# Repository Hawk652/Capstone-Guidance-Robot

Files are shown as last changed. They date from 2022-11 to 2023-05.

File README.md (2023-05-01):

# Greeting and Guidance Robot

## Executive Summary

Entering a building for the first time can be confusing. An insuffieicnt amount of information is typically provided to help one traverse a new building. With the new Ashraf Islam Engineering Buidling that is currently being built for Tennessee Technological University, the same issues will occur. The focus of the capstone project is to provide a solution to the problem. The solution is a autonoumous greeting and guidance robot that will assist people in navigating the Ashraf Islam Engineering Building. 

## Capabilities

Our final product is capable of mapping and navigating an area whilst avoiding collisions. It can reroute its path and always ensure that the user gets to the room that they are wanting to go to as well as return to its starting location once it's finished.

## Salient Outcomes

We learned that bluetooth 5.2 location services is not very accesible at the consumer level as of yet outside of heavy research or recent products. It's the reason why we ended up having to change to ultra wideband triangulation for location verification. We're also going to be learning about and implementing near field sensors as close range location verification with the assistance of Dr. Charles Van Neste More stuff will get added as we actually assemble the project.

## Project Demonstration

[Video demonstration of our Capstone project!](https://youtu.be/Icbw_ISEM2E)

## About Us

### Team
[Samuel Mandody](
https://www.youtube.com/watch?v=M5V_IXMewl4) - Knowledgeable in Embedded Systems. Strong fundamental coding skills and quick learner. Will be working on the locomotion subsystem and everywhere else coding related.

[Gabriel Kim](https://www.youtube.com/watch?v=dQw4w9WgXcQ) - Electrical engineering major with a focus on smaller electronics. Working mainly on the main control subsystem.

Emma Brown - Enjoys designing and implementing hardware. Willing to research and a fast learner. In charge of the safety subsystem.

[Andre Nguyen](https://www.youtube.com/watch?v=l60MnDJklnM) - Electrical Engineering major with a focus on power. In charge of the power subsystem. The designated team leader.

[Jacob Wilkinson](https://www.youtube.com/watch?v=GQHVQvePdtI) - Electrical and Computer Engineering major with a focus on embedded software development. In charge of user interface.

### Faculty Supervisor

Dr. Charles Van Neste

### Stakeholders

Dr. Andy Pardue is the customer and individual who came up with the idea for this project. Occupants of the Ashraf Islam Building alike will benefit from the guidance robot. 

### Recognitions 

A special thank you to:
Tristain Hill for providing us with the Turtlebot

Dr. Stephen Canefield for assisting us with the software implementation of the robot.

## Repo Organization

### [Reports](https://github.com/Hawk652/Capstone-Guidance-Robot/tree/main/Reports)
The section contains the project proposal documents and the conceptual design and planning documents.

### [Documentation](https://github.com/Hawk652/Capstone-Guidance-Robot/tree/main/Documentation)
The section contains the 3D models, electrical files, images related to the project, and signoffs.
#### [3D Models](https://github.com/Hawk652/Capstone-Guidance-Robot/tree/main/Documentation/3D%20Models)
#### [Electrical](https://github.com/Hawk652/Capstone-Guidance-Robot/tree/main/Documentation/Electrical)
#### [Images](https://github.com/Hawk652/Capstone-Guidance-Robot/tree/main/Documentation/Images)
#### [Signoffs](https://github.com/Hawk652/Capstone-Guidance-Robot/tree/main/Documentation/Signoffs)

### [Software](https://github.com/Hawk652/Capstone-Guidance-Robot/tree/main/Software)
The section will contain all software related to the project.

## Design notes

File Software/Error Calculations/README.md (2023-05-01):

# Error Calculations for Trilateration
## Function
This script runs a random amount of points in a range and calculates the error of the robot at that location. This assumes a specific placement of beacons and requires that the max error for each beacon is 10cm. The error is calculated for many points and the max error for all tested points is shown. This should prove the accuracy of the system.
## Dependencies
The only dependencies for this software is the default Matlab libraries
## How to Install
Matlab can be downloaded from the Mathworks website: https://matlab.mathworks.com/
Once downloaded, run the executable.
## How to Run
Run using the run button in Matlab's editor tab.

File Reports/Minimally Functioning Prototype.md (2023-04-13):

# Minimally Functioning Prototype

## Locomotion
Enclosures for the new stepper motors were designed and printed. Unfortunately, the new stepper motors will not be utilized because the motor controllers will not be arriving in on time.

## Safety
The robot is able to prevent collision with an object or wall.

## Localization
ESP32 beacons were able to communicate with each other and relay positional data. The ESP32 beacons were used instead because the ultra-wideband beacons will not be arriving in on time. 

## Power and Charging
The chaging subsystem is able to transform AC power from a receptacle into DC power and deliver it to the robot's power subsystem. The buck converters in subsystem is able to deliver 12 V at the output. However, the power subsystem will not have the desired battery due to ordering issues. 

## User Interface
The robot is able to move around and change directions with the use of voice commands through a microphone.

## Main Control
The robot is able to take commands from the user interface subsystem and use the LIDAR and motors to move around in its environment.

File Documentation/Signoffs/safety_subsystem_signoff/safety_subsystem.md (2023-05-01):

# Safety Subsystem

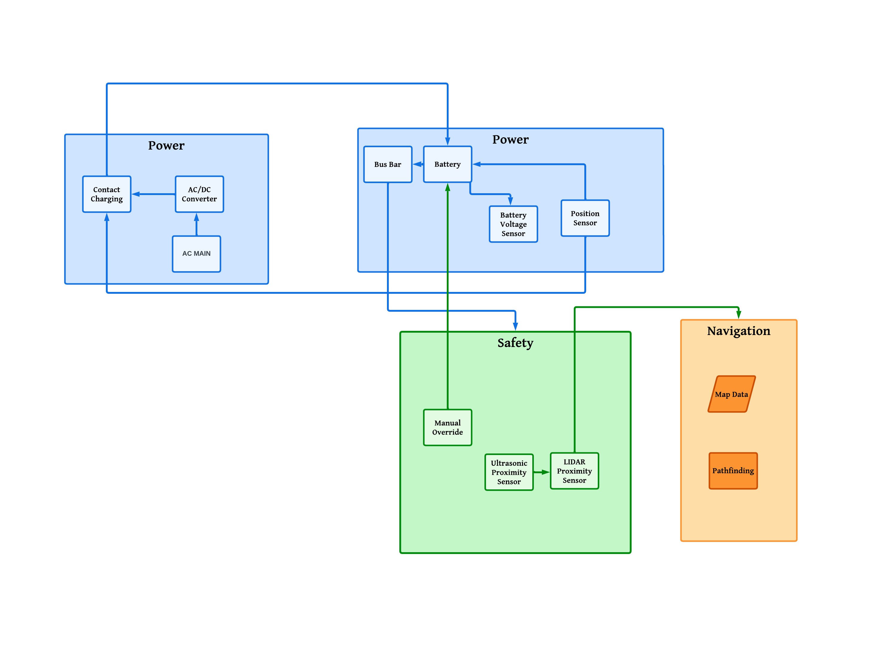
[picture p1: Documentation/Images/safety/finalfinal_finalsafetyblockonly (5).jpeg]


#  Function of the Subsystem

 The safety Subsystem will be tasked with obstacle avoidance, a manual override, and utilizing the LIDAR’s mapping capabilities. The sensors and button will be attached to the top of  the robot, that way it can utilize “seeing” capabilities. The sensors will gather information within the range (0.5 meters) of  robot and send this information to the Arduino or Raspberry PI.  To ensure that there will be no obstacle undetected, the LIDAR and Proximity sensor, ultrasonic  will be utilized to ensure redundancy. When an obstacle is detected within the range by the proximity sensor, ultrasonic sensor and the LIDAR, the information will be transmitted to the Main Control subsystem.  The LIDAR will be using its mapping capabilities to determine if the robot is too close to walls, doors, and corners. The proximity sensor will be using a 360 obstacle avoidance technique to determine the location of the obstacle. The DDS module will take the signal from a crystal oscillator and use it as a clock to create a buffer output waveform at a specific frequency that is set by the onboard microcontroller.  The Grove - Ultrasonic Distance Sensor will be using a range of  3cm - 350cm by using a non-contact form of measurement. 

#  Constraints
| No. |Constraint  |  Origin  |
|-|-|-|
|1|  Shall have manual override (power will be cut from the motor) |Supervisor: Dr. Van Neste |
|2 |Shall maintain a distance of 0.5 m from obstacles and people |Broader Implication |

#  Buildable Schematics
##  Subsytsem Schematic

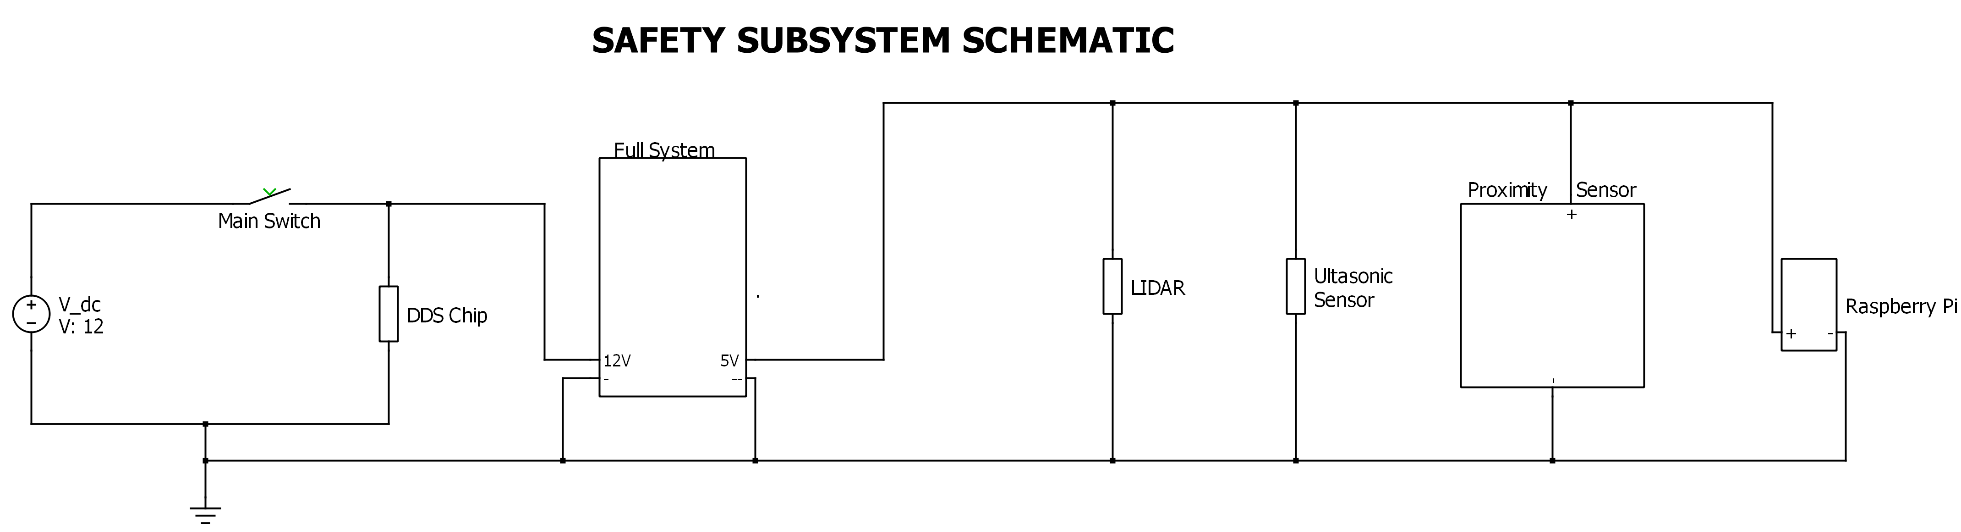
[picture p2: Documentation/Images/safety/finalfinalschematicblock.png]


This schematic illustrates all the components that will be interacting with one another in this system. Each of these sections will be covered throughout this document. 

## Pinout of the Subsystem
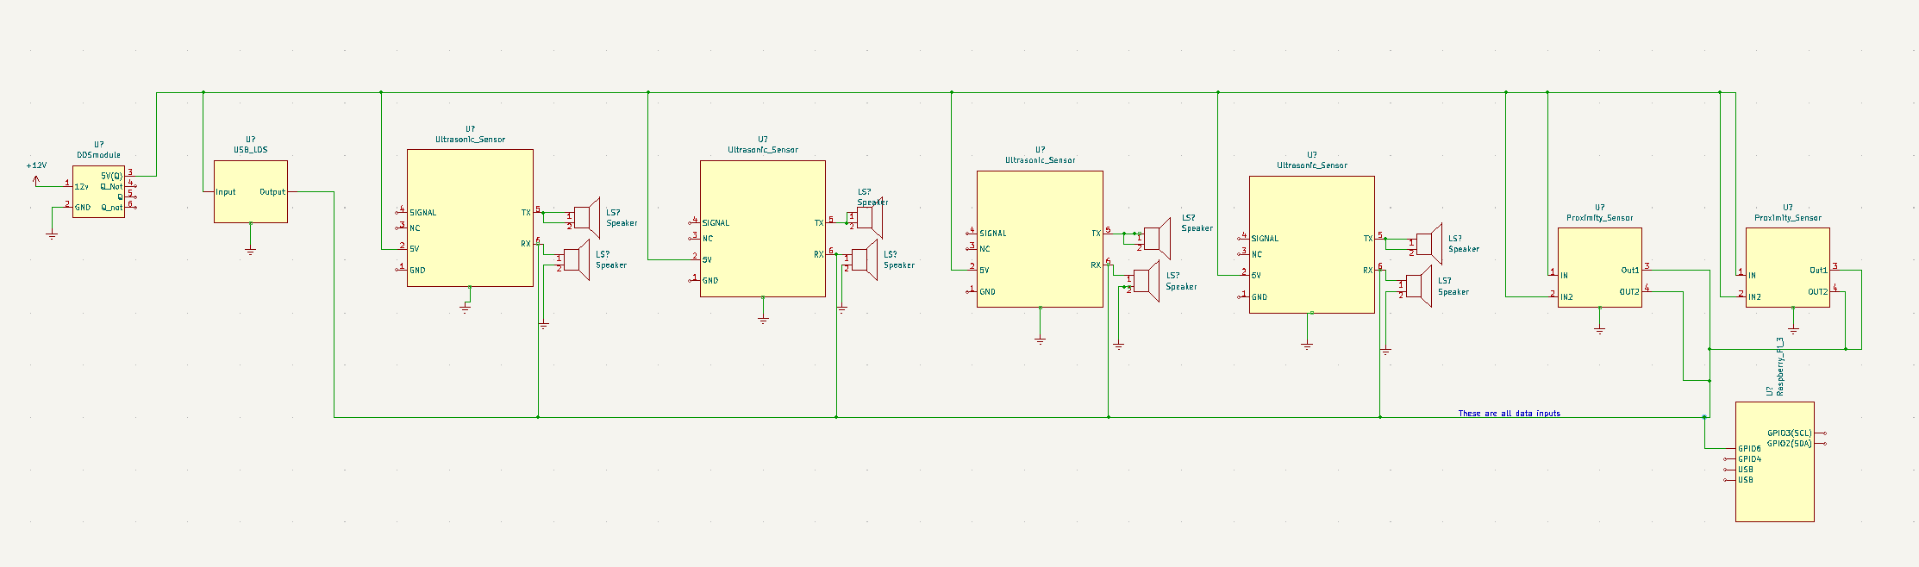
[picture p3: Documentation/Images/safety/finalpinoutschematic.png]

##  Near Field Sensor (Proximity Sensor)
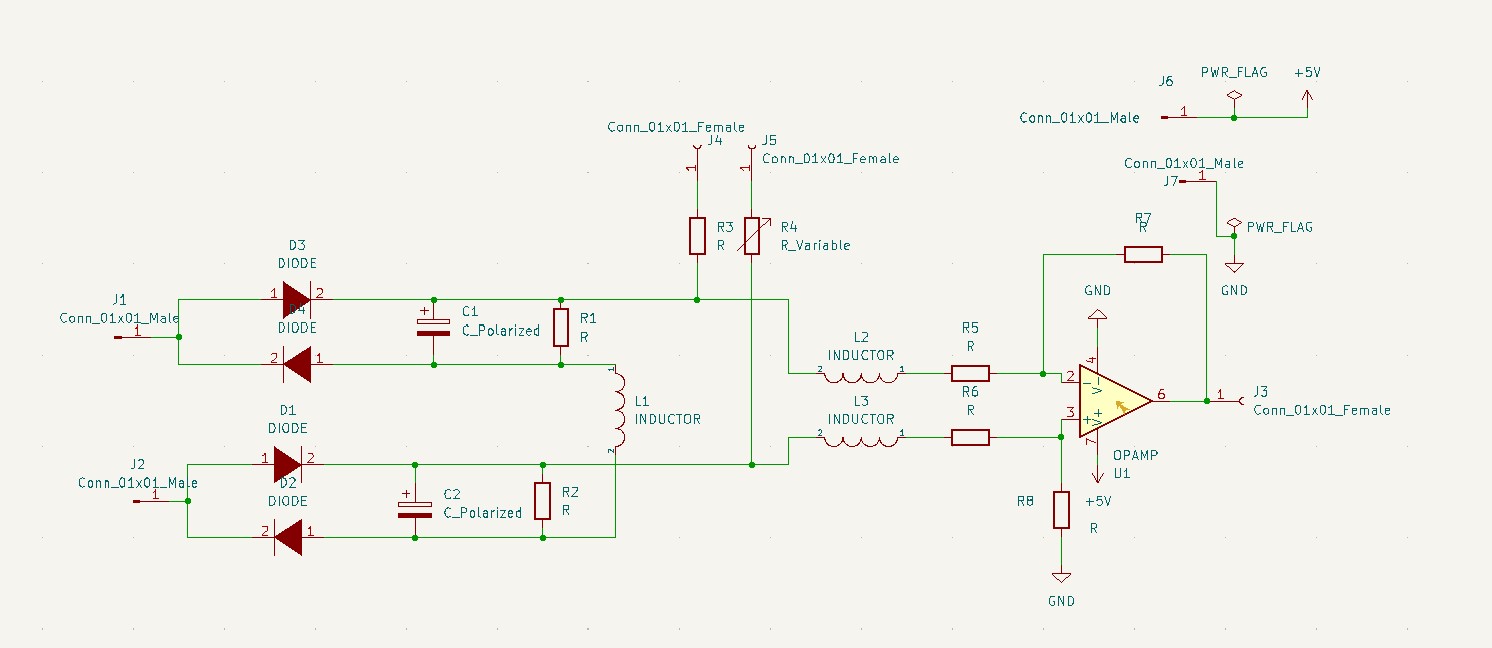
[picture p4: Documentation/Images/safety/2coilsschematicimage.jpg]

The Proximity Sensor will be the main safety sensor for this subsystem. This sensor will be able to detect objects in an omnidirectional field of view. This sensor will be accomplished by the implementation of coils. By using their electric fields, the sensors will be able to detect very small changes in their distance. Below are the specific values that will be used for each component and are necessary for the sensor to function properly. These specific values have been researched in “Capacitive omnidirectional position sensor using a quarter wave resonator,” and discussed with Dr. Van Neste to ensure that these should be correct. 

### Table of Components 
|Component| Value| Unit|
|-|-|-|
|D1-D4 |1N4001|-|
|C1,C2  |4.7|μF|
|R1,R2| 1|kΩ|
|L1,L2,L3 |300|μH|
|R4,R5 |2|kΩ|
|R6,R7 |20|kΩ|

## Image of PCB 
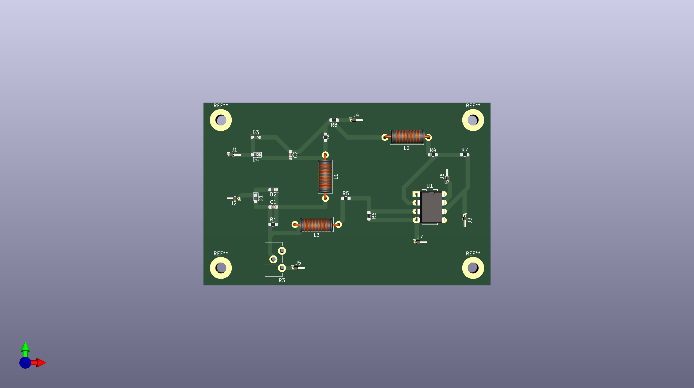
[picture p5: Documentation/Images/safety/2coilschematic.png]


front side
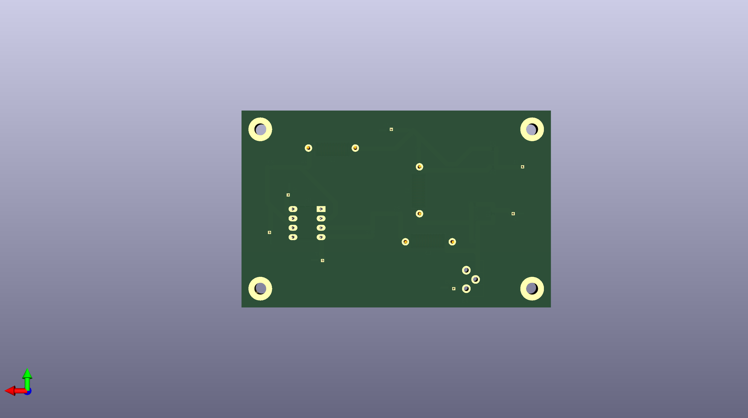
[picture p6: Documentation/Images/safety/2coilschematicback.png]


back side

### 3d Model of Attachement to Robot
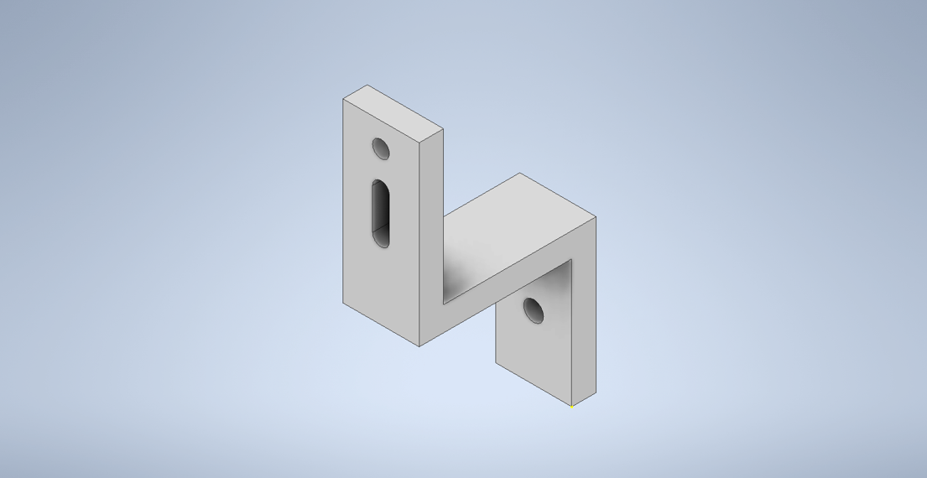
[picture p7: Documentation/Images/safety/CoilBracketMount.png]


### Reasoning for Proximity Sensor
After extensive research and discussions with Dr. Van Neste, this sensor seemed to be the best for the Autonomous Guidance Robot. Currently, there are not any sensors on the market that would be within the price range of this project. The best option was to build an omnidirectional sensor with the help of Dr. Van Neste. This sensor will enable the robot to detect any obstacles or people that might stand in the way of the robot and be able to avoid the detections that have been obtained. 

#  Ultrasonic Sensor
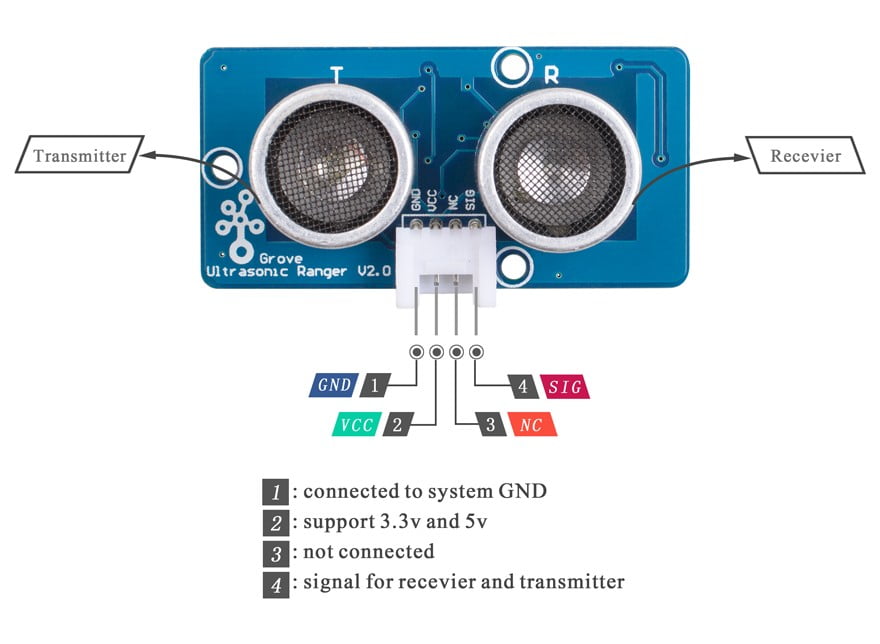
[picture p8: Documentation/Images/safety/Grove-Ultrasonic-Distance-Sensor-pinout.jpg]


The Grove - Ultrasonic Distance Sensor will be implented as the ultrasonic sensor for this subsystem.This item will be a backup sensor for the Proximity sensor. 

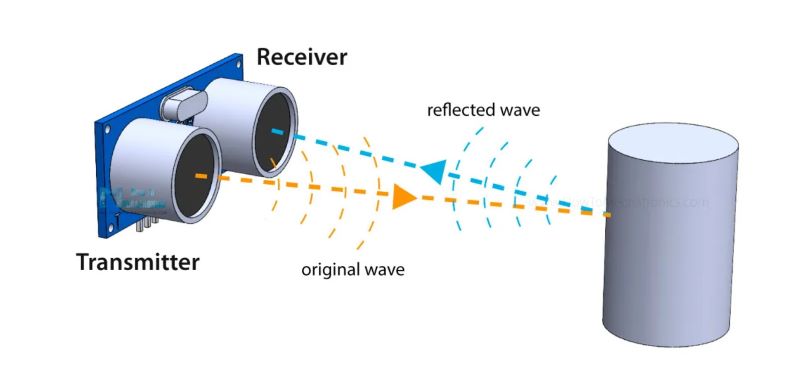
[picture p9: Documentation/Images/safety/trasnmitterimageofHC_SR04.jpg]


The reasoning for this is because the Proximity sensor will have a better range and has a radial sensing method than the ultrasonic sensor. The ultrasonic sensor determines an object's distance by sending a form of sonar waves out and determines the distance from the receiving signal that reflects off of an object that is within the range of the sensor, which is 3cm to 350cm. 

## Pinout of Ultrasonic Sensor
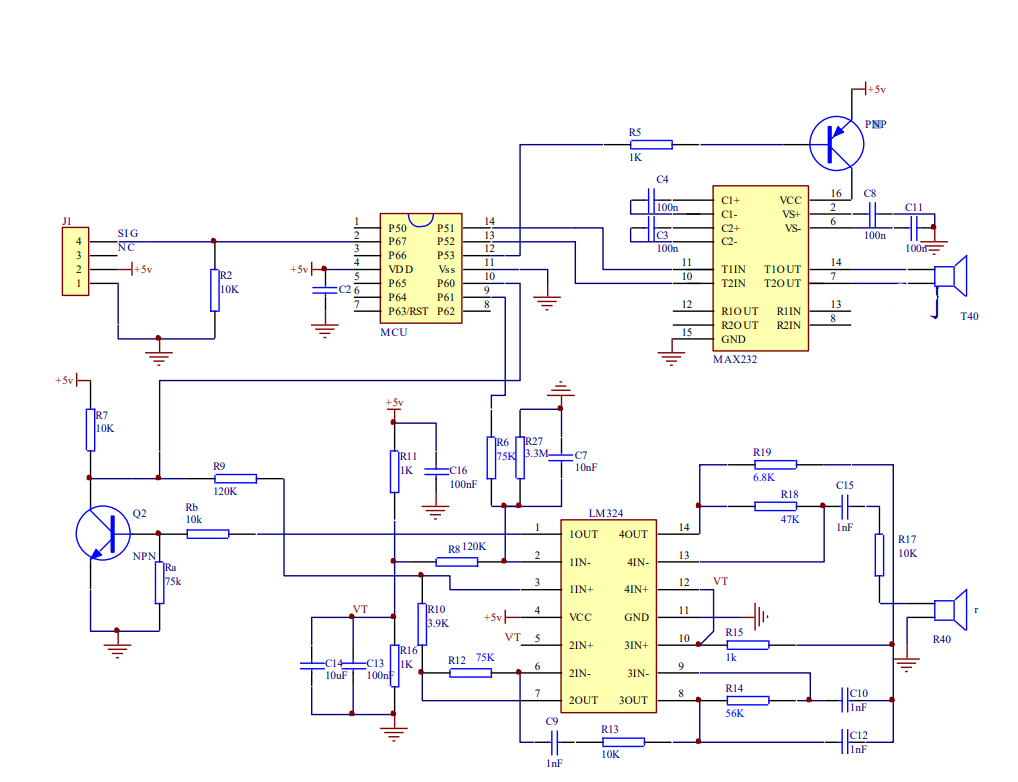
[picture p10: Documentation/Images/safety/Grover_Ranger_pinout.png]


|Component| Value| Unit|
|-|-|-|
|Operating Voltage|DC 3.2~5.2V|-|
|Operating Current |8|mA|
|Operating Frequency| 40|KHz|
|Min Range |3 |cm|
|Max Range |350|cm|
|Accuracy|2|mm|
|Measuring Angle |<15|°|
|Dimmension|50 x25 x16|mm|
 
# DDS Module 
The DDS module is going to create a sinusoidal wave to get the coil to resonate. This module will generate a sine waveform then this signal will be sent to the coil.

# LIDAR
The LIDAR component will be implemented for the robot's safety and surroundings. The LIDAR will determine where the walls, corners, and doors are. The robot will be aware of the floor layout and will be able to differentiate obstacles compared to structures. The details on how this device works and how it will be implemented in the rest of the system will be in the Localization Subsystem.

# Raspberry Pi
The brain of the robot will be the Rasperry Pi. This means that all of the components in this subsystem will send all of their information back to the Raspberry Pi. The details on how this device works and how it will be implemented in the rest of the system will be in the Main Control Subsystem.

# Main Switch

The main switch's functionality will be to quickly cut off power to the robot for emergency purposes. This switch wil be located on the outside of the robot that way the robot can be shut off manually. The switch will be discussed further in the Power Subsystem.

#   Analysis

The safety Subsystem (SubsystemBlockDiagram) is a schematic of how the subsystem will connect with one another and to the Main control subsystem. The main switch will be connecting directly to the Battery (12V), this will turn off everything in an event of an emergency. The DDS module runs off of the same voltage and will go through a DC/DC converter to reduce the voltage to be 5V.  Once the voltage as been converted to 5V the power of  the rest the Safety subsystem. The LIDAR,
Grove - Ultrasonic Distance Sensor, Proximity Sensor, and the Raspberry Pi will be all be connected  in parallel with one another. The LIDAR is further discussed in detail within the Localization subsystem. The Grove - Ultrasonic Distance Sensor is used to ensure that the robot will detect an object within a range of 3cm - 350cm. The output of the subsystem will be sent to the Raspberry Pi. The proximity sensor will be using three electric magnetic resonators to detect changes in the electric field. By using the electric field sensor it can detect objects in close proximity, therefore creating a collision avoidance sensor.  

#    BOM
|Item| Quantity| Price Per Item| Total Price
|-|-|-|-|
|DDS Module |4|$50|$200 | |
|Grove - Ultrasonic Distance Sensor  |4|$3.95| $15.80 |
|LDS-01(LIDAR)| 1 |$200|Already Purchased
|Copper Wire |1|$54.82| $ 54.82  |
|Raspberry Pi |1|$35 |Already Purchased  |
|Total Price|||$270.62|
#    Reference

“Capacitive omnidirectional position sensor using a quarter wave resonator,” IEEE Xplore. [Online]. Available: https://ieeexplore.ieee.org/document/9827944. [Accessed: 21-Nov-2022]. 

“Data Sheet - SparkFun Electronics.” [Online]. Available: https://cdn.sparkfun.com/datasheets/Sensors/Proximity/apds9960.pdf. [Accessed: 22-Nov-2022]. 

“Grove - ultrasonic distance sensor,” Seeed Studio, 29-Dec-2022. [Online]. Available: https://www.seeedstudio.com/Grove-Ultrasonic-Distance-Sensor.html. [Accessed: 03-Feb-2023].

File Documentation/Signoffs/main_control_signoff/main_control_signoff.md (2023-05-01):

# Main Control Subsystem

## Functionality of the Subsystem
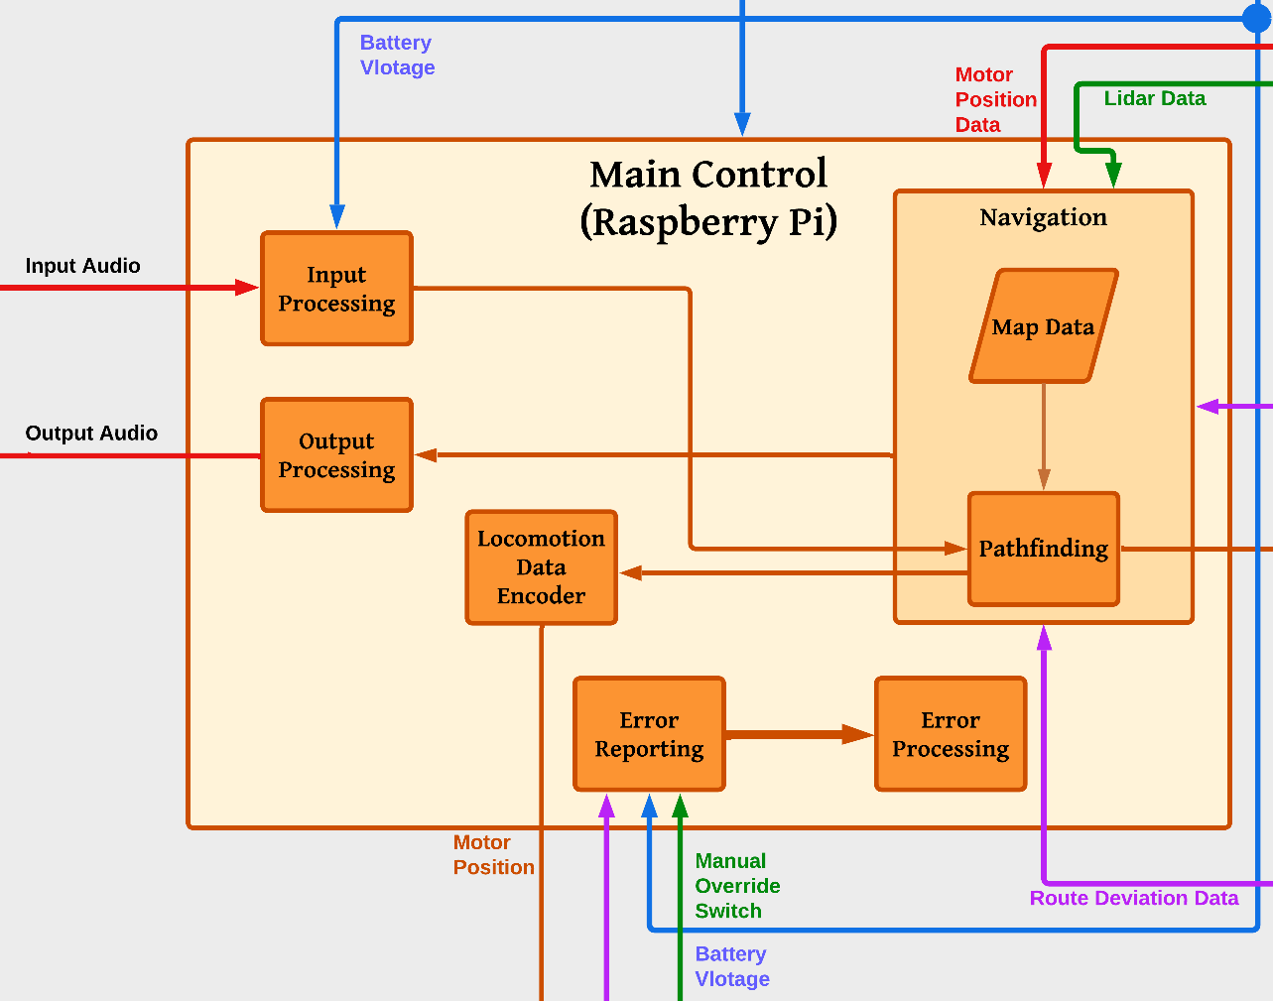
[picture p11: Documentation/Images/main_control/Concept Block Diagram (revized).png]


The main control subsystem's function is to receive inputs from the AuR's other subsystems and use those inputs to determine the AuR's actions. The subsystem is responsible for navigation and pathfinding as well as connecting all of the subsystems together.

## Specifications and Constraints
| No. | Specifications and Constraints | Origin |
|-|-|-|
| 3 | Shall operate on one floor only | Supervisor: Dr. Van Neste |
| 6 | Shall not operate below 15-20% of the battery capacity | Ethics |

## Buildable Schematic
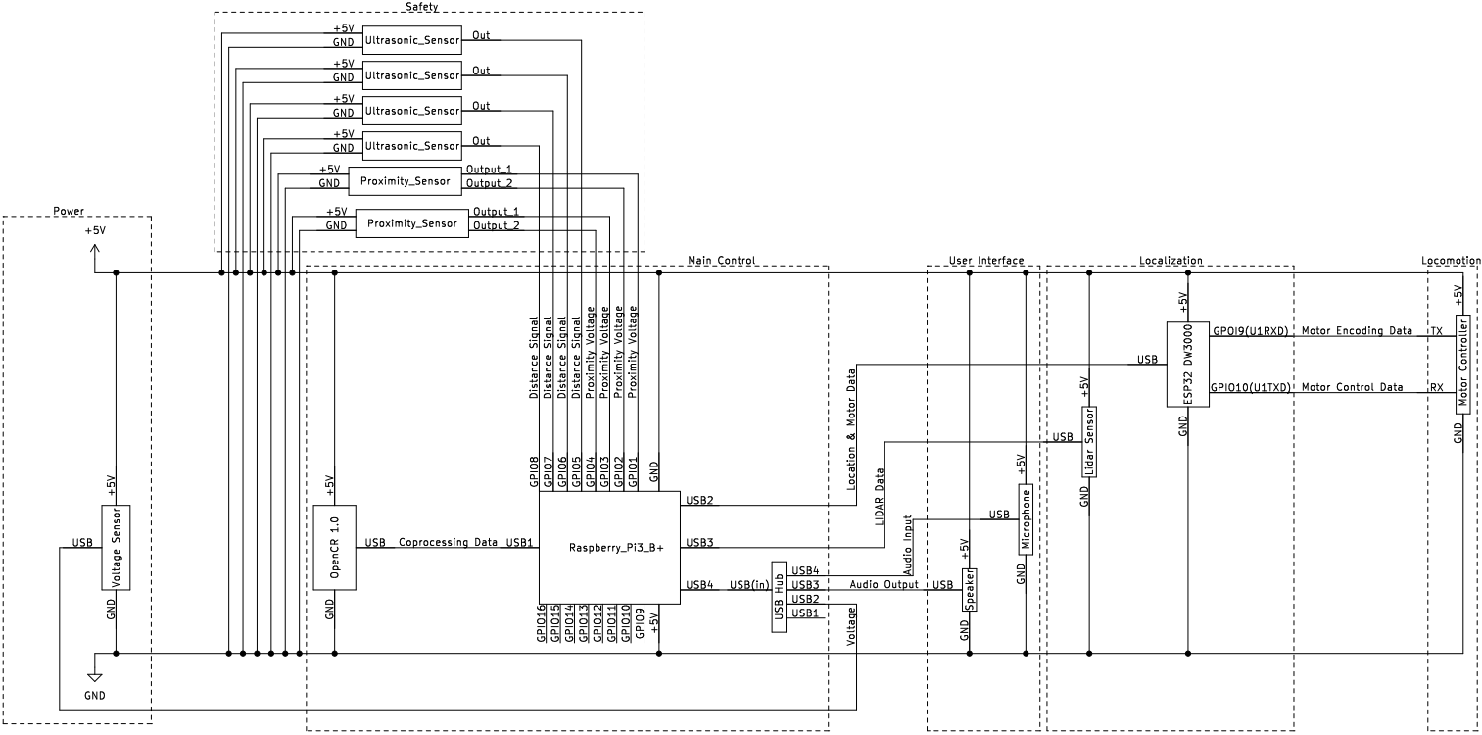
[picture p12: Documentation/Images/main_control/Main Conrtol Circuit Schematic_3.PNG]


## Analysis

### Flow Chart
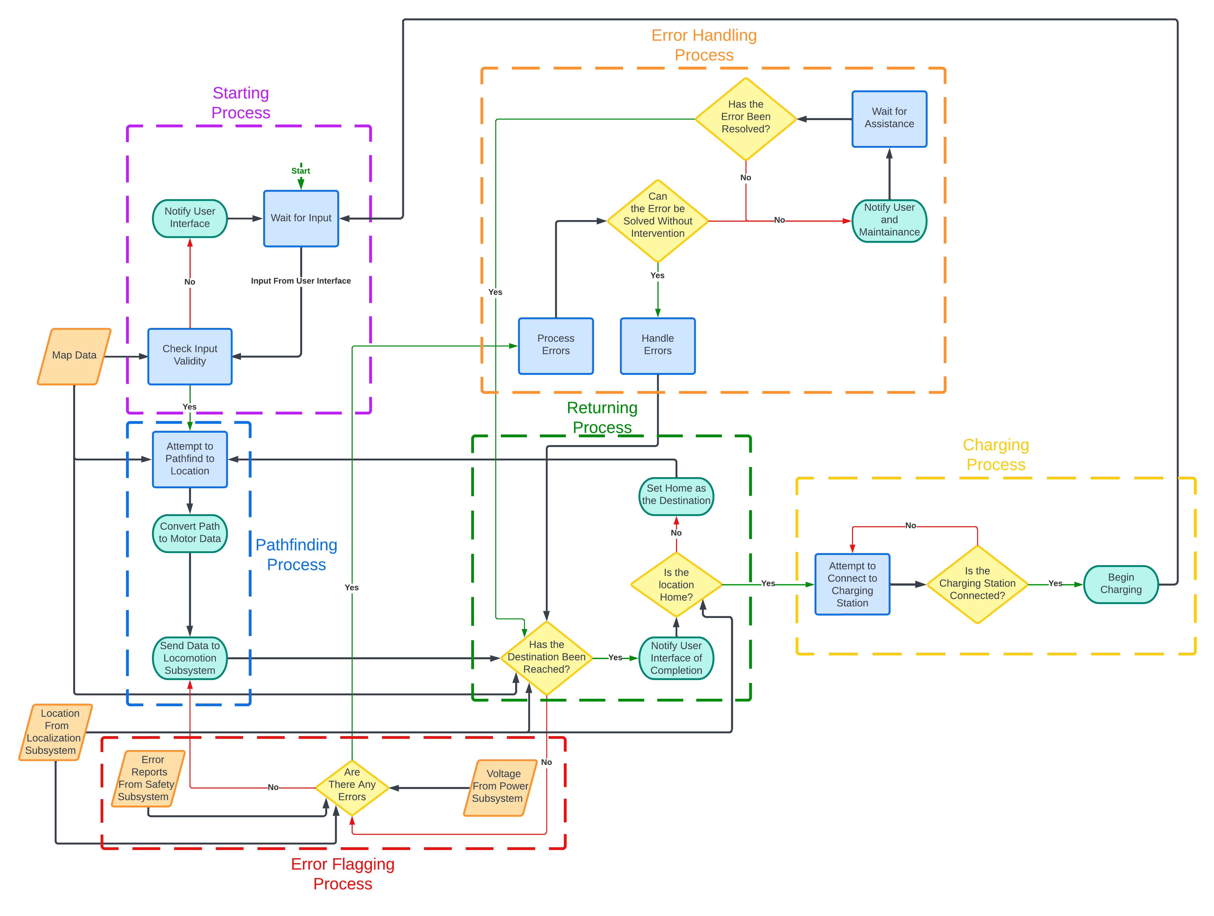
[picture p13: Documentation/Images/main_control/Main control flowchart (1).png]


### Navigation
The main control will receive location data and route deviation data from the localization subsystem as well as locomotion data from the rotary encoder. This data will be used to build and update a map model of the building. The user input will be processed in conjunction with the localization data to construct a path from the AuR's location to its desired destination. This will take place using tools provided by the ROS2 OS.
### User Input/Output
The main control will receive an input from the user interface subsystem and process that input into a usable format. The processed data will be a destination which the main control will use for its pathfinding process. An output is generated based on the status of the AuR and sent to the user interface subsystem.
### Error Processing
The main control will receive inputs from the safety, localization, and power subsystems. It will compare these inputs to expected values and if there is a discrepancy, an error will be reported. The error or errors will then be processed and a course of action will be determined based on number of errors, error details, severity of errors, and other data provided to or processed by the main control subsystem.
### Power
The Raspberry Pi3 B+ is connected to 6 devices via the four usb ports with a usb expansion port as well as 8 devices via the GPIO pins. Current output for each of the four onboard usb ports is limited to 500mA meaning the maximum output for four ports together would be 2A, however total current draw from all usb ports is limited to 1.5A[1]. GPIO pins can safely draw 50mA meaning the maximum output for 8 pins togeter would be 400mA or 0.4A. A total current draw of 2A and a voltage of 5V results in a 10 Watt load, which is doubled in order to ensure adequate battery life. This means the power subsystem must provide 20 Watts to the Main Control subsystem.
### OS
The Raspberry Pi3 B+ will be running a version of ROS2 Foxy which is based on Ubuntu 20.04. While the specific hardware requirements are not listed, the version used is a custom image provided by Robotis explicitly for use with the Raspberry Pi 3 B+[2].

## BOM
| Item | Quantity | Price Per Item | Total Price |
|-|-|-|-|
| Raspberry Pi 3 B+ | 1 | $35 | Purchased |
| USB Hub | 1 | $7.99 | $7.99 |
| | | Total Subsystem Cost: | $7.99 |

# References
[1]“Raspberry Pi Documentation - Raspberry Pi hardware,” www.raspberrypi.com. https://www.raspberrypi.com/documentation/computers/raspberry-pi.html#maximum-power-output (accessed Jan. 29, 2023).

[2]Y. Name, “ROBOTIS e-Manual,” ROBOTIS e-Manual. https://emanual.robotis.com/docs/en/platform/turtlebot3/sbc_setup/#sbc-setup

[3]“Raspberry Pi 3 Model B+.” [Online]. Available: https://static.raspberrypi.org/files/product-briefs/Raspberry-Pi-Model-Bplus-Product-Brief.pdf (Accessed: Nov. 20, 2022)

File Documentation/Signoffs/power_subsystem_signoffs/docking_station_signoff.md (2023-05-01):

# Docking Station Subsystem

## Function of the Subsystem
The function of the docking station subsystem is provide a area for the AuR to autonomously recharge power when needed.

## Specifications and Constraints

| No. | Specifications and Constraints | Origin | 
|-|-|-|
| 1 | Shall have plugless charging | Supervisor: Dr. Van Neste 
| 2 | Shall follow proper wire gauging standards | NEC 310.16(b)

## Buildable Schematic 
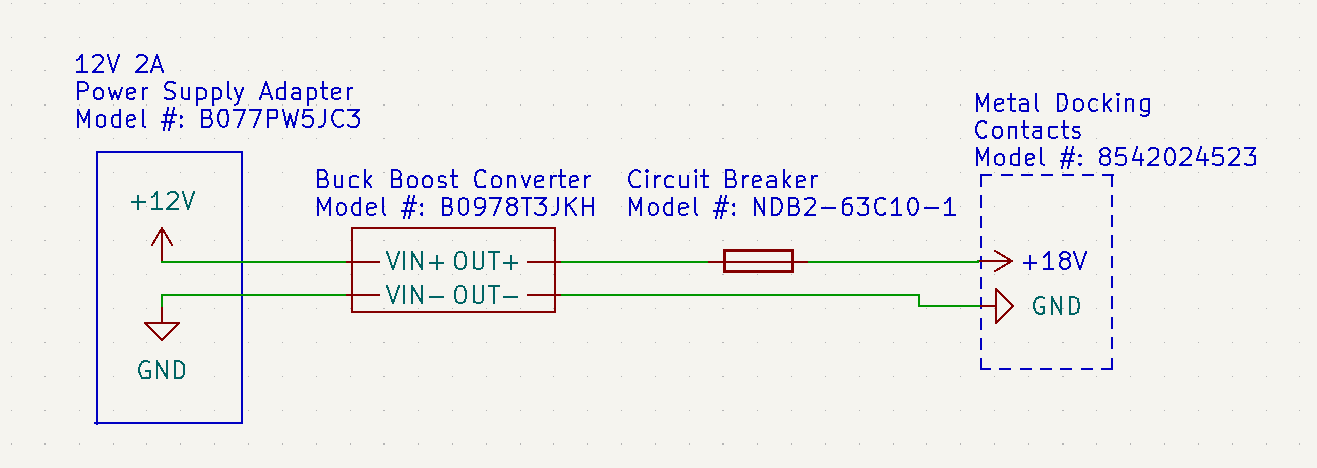
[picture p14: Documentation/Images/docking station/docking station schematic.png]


The docking station subsystem will recieve power from a 120 VAC receptacle. The 120 VAC will be converted into 12 VDC through the use of a power supply AC adapter. The 12 VDC will then be sent to buck booster to be step up to 18 VDC to match the battery voltage. Then the 18 VDC is sent to the metal contacts for the AuR to recieve power. A circuit breaker is added in to provide overcurrent protection to the circuit in the case of a short circuit happening. The buck booster converter has a functioning switch implemented which allows a user to cutoff power to the metal contacts. 

The power supply adapter will feed into the circuit through a hole on the side of the docking station's box wall. The circuit breaker  will be mounted using velcro so it does not move around. There is enough room in the box to house the breaker. A hole is created in the lid of the docking station to provide a place for the buck boost converter to mount. This will allow a user to adjust the buck boost converter and switch the circuit on and off with ease. There are two 19 mm x 15 mm holes for the metal docking contacts to be placed in.  

#### 3D Model of Charging Station
The docking station follows the same idea as receptacles by having two indentations to house the active metal contacts within the docking station. By having the metal contacts embedded into the docking station, it would be more difficult for users and other objects to accidentally touch both active metal contacts. The indentations additionally assist in guiding the AuR into the correct position when recharging. A wire can fed through a hole on the side of the charging station and reach the metal contacts from within the docking station.

##### Front Isometric View
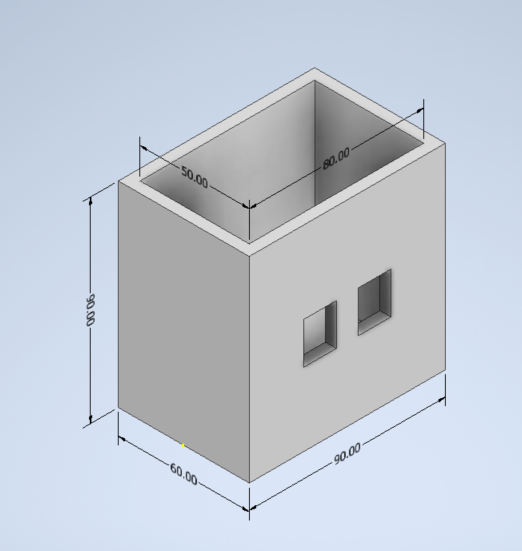
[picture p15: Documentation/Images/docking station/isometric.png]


##### Front View
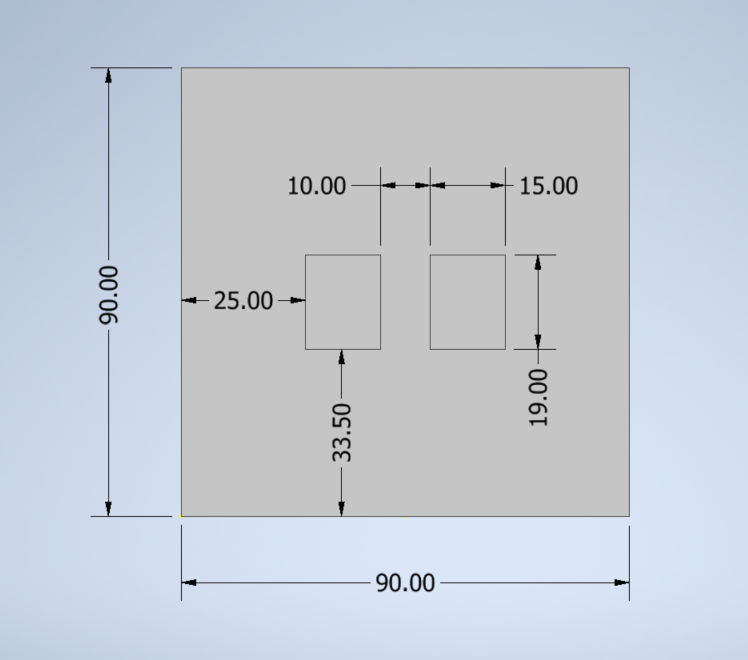
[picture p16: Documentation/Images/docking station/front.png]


##### Back Isometric View
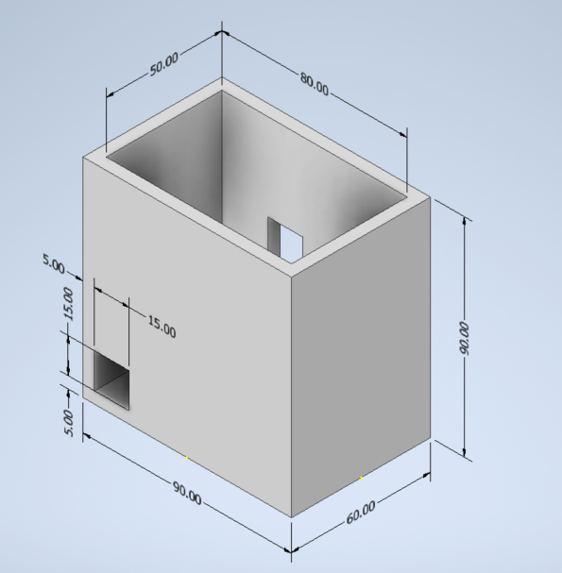
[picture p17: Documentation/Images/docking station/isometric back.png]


#### Lid Isometric View
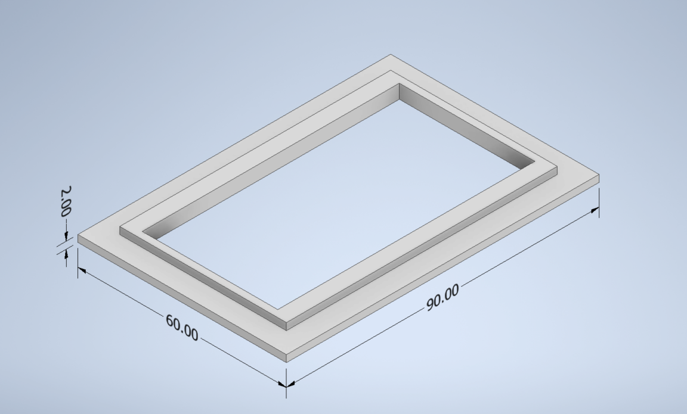
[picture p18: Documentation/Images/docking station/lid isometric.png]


#### Lid Top View
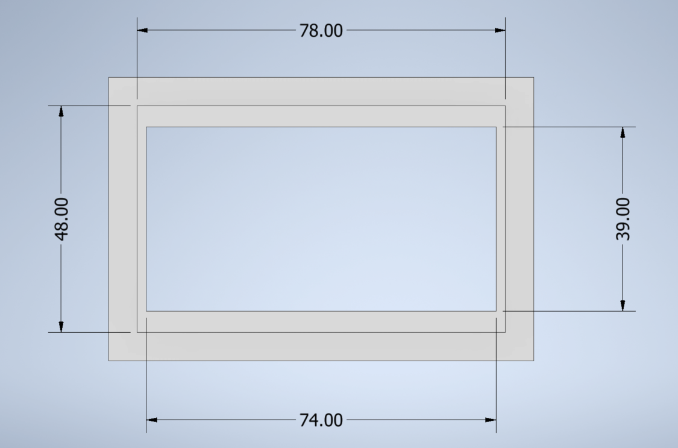
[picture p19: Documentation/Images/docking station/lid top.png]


#### Lid Side View
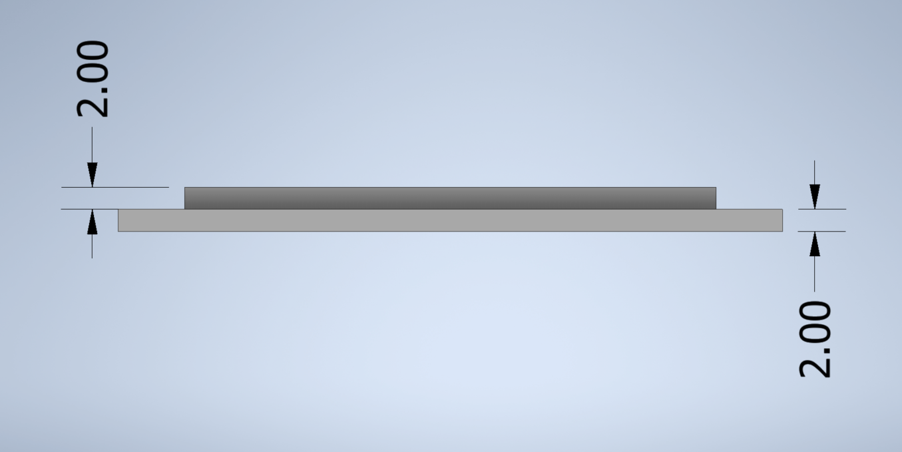
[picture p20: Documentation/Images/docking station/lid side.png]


## Analysis
The current dimensions are based on the componenets designed to be used and the turtlebot's current height and width. The charging box may be adjusted in the future to accomodate any modifications to the turtlebot's dimensions. A 12V Allkpoper circuit breaker is added to provide overcurrrent protection in the case that a short circuit occurs between the metal contacts. Furthermore, the Allkpoper circuit breaker can easiy be reset instead of having to replace the fuse whenever the breaker is tripped. A buck boost converter will add further protection to the system and provides a switch to operate the circuit. Arc flash shall not occur due to the metal contacts only being supplied 12VDC. Additionally, there is sufficient distance between the metal contacts and a circuit breaker to prevent arc flash from occuring. 

## BOM
| Item | Quantity | Price Per Item | Total Price |
| --- | --- | --- | --- |
| 12V 2A Power Supply AC Adapter| 1 | $11.75 | $11.75 |
| Metal Contacts | 1 | $16.95 | $16.95 |
| Allkpoper Circuit Breaker | 1 | $12.90 | $12.90 |
| Boat Rocker Switch | 1 | $ 5.99 | Bought through the power subsystem|
| Buck Boost Converter | 1 | $ 20.88 | $ 20.88 |
| | | Total Subsystem Cost: | $62.48 |

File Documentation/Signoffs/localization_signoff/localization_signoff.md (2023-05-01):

# Localization Subsystem
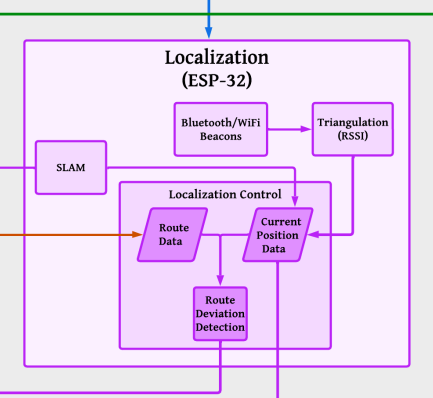
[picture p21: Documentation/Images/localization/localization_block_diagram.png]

## Function of the Subsystem
The localization subsystem (Fig. 1) will be tasked with gathering and processing positional data points from sensors. The sensors shall all be mounted onboard the Turtlebot 3. The sensors that will gather data for this subsystem will be the LIDAR and the ESP32UWB DW3000. The LIDAR will gather data points from all reflective surfaces around it for the SLAM algorithm to determine the AuR's current location. The UWB (Ultra Wideband) module will determine the distance between itself and 2 other UWB modules using triangulation. The other 2 UWB modules will serve as a destination marker. Using all the prior mentioned data, the AuR will be able to determine its current location. The AuR will use the updated current position data along with the route data generated from the navigation subsystem to determine the deviation of the route. 

## Specifications and Constraints

| No. | Specifications and Constraints | Origin | 
|-|-|-|
| 1 | Shall guide users to within 1 m of their desired room | Supervisor: Dr. Van Neste 
| 2 | Shall not deviate from the expected path by more than 15 cm | Broader Implication
| 3 | Shall detect the AuR's position to a precision of 15cm | Customer: Dr. Andy Pardue

## Buildable Schematic
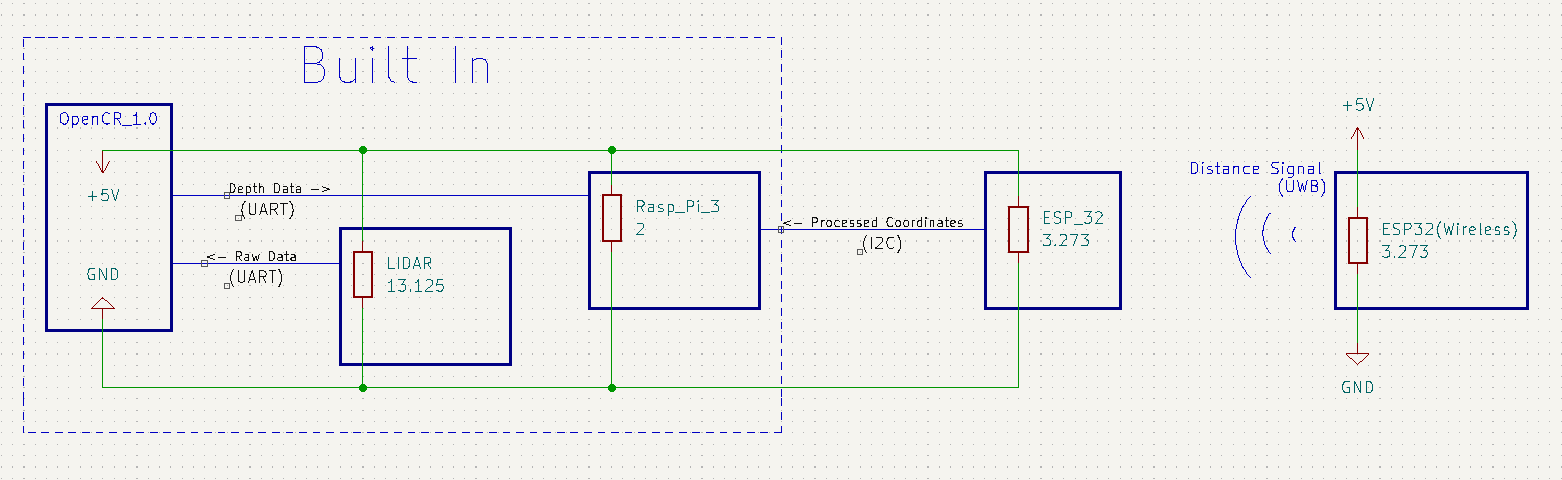
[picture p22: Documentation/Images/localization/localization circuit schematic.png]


The values for required voltage and resistive load used in Fig. 2. were derived from the specification documents for the individual components.

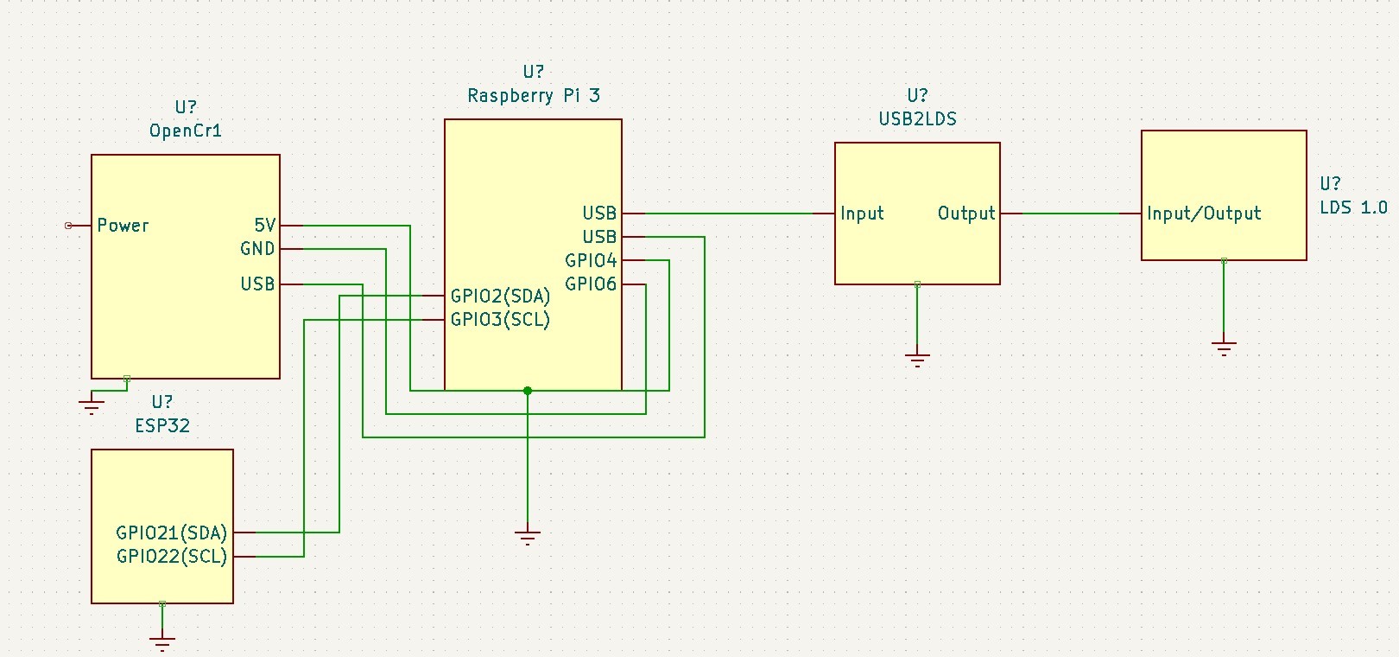
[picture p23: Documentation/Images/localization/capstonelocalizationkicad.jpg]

The image shows the connections between the components of the localization subsystem.

### Beacon
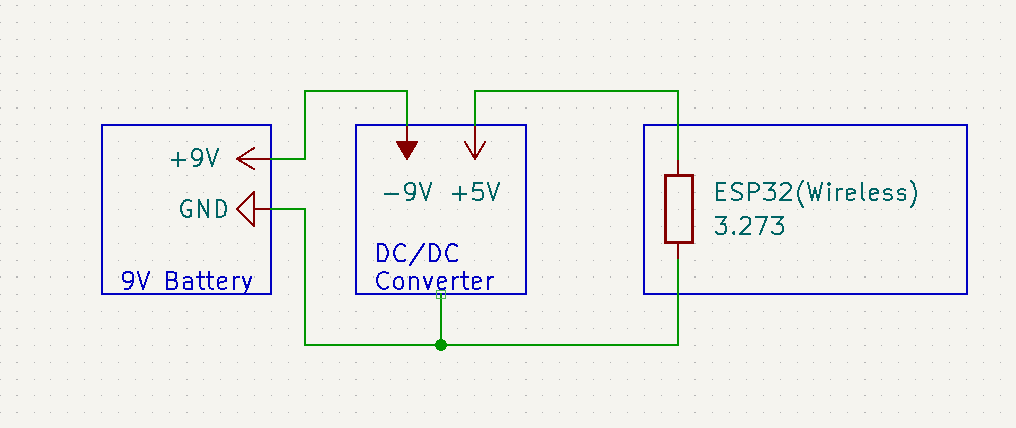
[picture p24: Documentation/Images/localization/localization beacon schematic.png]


The schematic only consists of power connections since all the data will be transmitted wirelessly to the main ESP32UWB DW3000 on the AuR. The beacon will have a onboard program that will continuosly verify the location of the AuR in near real time.



Dimensions are approximate. We were unable to find precise dimensions directly from the manufacturer, so we estimated them from the manufacturer-provided PCB schematic.





Here are the 3d models for the housing unit of the beacons. The dimensions of the housing unit is 19.3 x 8.15 x 7.62 $cm^3$. The housing unit will contain a breadboard, a 9v battery, a 9v to 5v dc to dc converter, and an ESP32 UWB development board.



The figure shows the beacons will be placed a little above the door frames in hallways. The beacons will be about 2 m from the floor. The housing units for the beacons will be attached to the wall using command strips. 

### Code Flowchart
Flowchart

The above figure is a flowchart showing the general functionality of this subsystem's software. When the AuR is turned on, the localization subsystem initializes itself and validates that all components are responsive. Once it has done this, it waits for a localization request from the main control. When a localization request is receieved, the localization subsystem estimates the AuR's position using the LIDAR and a SLAM, Simultaneous Localization And Mapping, algorithm. Once this is complete, the subsystem finds the RSSI, the Received Signal Strength Indicator, of nearby ultra-wideband beacons in order to triangulate its position in relation to those beacons. Once both localization methods are complete, the localization subsystem will compare the two results. If the results disagree, the localization subsystem will recheck its position using both method. Once both results agree, the localization subsystem will send the location data back to the main control and wait until another request is received.

## Analysis

### UWB  Beacons:


A UWB beacon-based solution was chosen for higher resolution localization since it is accurate to within 15 cm which aids the constraints of being within 15 cm of its path and within 1 m of its destination [1]. The UWB beacons will be ESP32 UWB DW3000 modules.

Trilateration can be used to find the coordinates of an object based on its distance relative to three beacons [2]:

$(x- x_{1})^{2}+(y- y_{1})^{2} = r_{1}{}^{2}$

$(x- x_{2})^{2}+(y- y_{2})^{2} = r_{2}{}^{2}$

$(x- x_{3})^{2}+(y- y_{3})^{2} = r_{3}{}^{2}$

In order to find the distance from the device to a given beacon this Two Way Ranging(TWR) equation is used, where c is the speed of light d is the distance from the given beacon, RR is the Received Response time, Poll Sent time, SR is the Sent Response time, RP is the Received Poll time, RF is the Received Final time, SF is the Sent Final time and ToF is the Time of Flight [3]:

$ToF=\frac{(RR-SP)-(SR-RP) +(RF-SR)-(SF-RR)}{4}$

These equations work by calculating the time between messages and using the speed of light to determine the distance between beacons. The coordinates are calculated by the ESP32 and sent from the ESP32 to the Raspberry PI via a wired connection using I2C protocol.

Based on the tests performed and documented by the articles "Performance Comparison between Decawave DW1000 and DW3000 in low-power double side ranging applications"[4] and “Design of  localization System Based on Ultra-Wideband and Long Range Wire-less,”[5] we can meet the constraint of having less than 15 cm of horizontal error. The DW3000 can be configured to operate on a range of channels which refer to the device's operating frequency and bandwidth. An error of 15 cm was achieved with the DW3000's channel 9 configuration. Channel 9 was chosen for its higher frequency which encounters less environmental interference and can therefore provide more acurate measurements when compared to other channels. Channel 9 has a frequency of 7987.2 MHz and a bandwidth of 499.2 MHz[6].

From the system of equations which define trilateration the following can be derived[7]:

$\Delta = x_1(y_2-y_3)+x_2(y_3-y_1)+x_3(y_1-y_2)$

$Ex = {1\over2\Delta}(y_3 - y_2)(2r_1e_1 + e_1^2 - 2r_3e_3 - e_3^2) - {1\over2\Delta}(y_3 - y_1)(2r_2e_2 + e_2^2-2r_3e_3 - e_3^2)$

$Ey = -{1\over2\Delta}(x_3 - x_2)(2r_1e_1 + e_1^2 - 2r_3e_3 - e_3^2) + {1\over2\Delta}(x_3 - x_1)(2r_2e_2 + e_2^2-2r_3e_3 - e_3^2)$

where $E_x$ and $E_y$ are the horizontal and vertical error of the hallway, $e_i$ is the distance error of the respective beacon, $r_i$ is the distance of the Aur from the respective beacon, and $x_i$ and $y_i$ are the horizontal and vertical coordinates assigned to the respective beacons. Since all distance errors are equal the equations can be simplified to:

$Ex = {1\over2\Delta}(y_3 - y_2)*2e(r_1 - r_3) - {1\over2\Delta}(y_3 - y_1)*2e(r_2 - r_3)$

$Ey = -{1\over2\Delta}(x_3 - x_2)*2e(r_1 - r_3) + {1\over2\Delta}(x_3 - x_1)*2e(r_2 - r_3)$

where $e$ is the $\pm10cm$ distance error provided in the data sheet[6]. Using the equations for $E_x$ and $E_y$ it is possible to find the totally error by using the equation:

$Total \ Error=\sqrt{E_x^2+E_y^2}$

After measuring a width of $238cm$ for the test area in Brown hall the following scenario was setup in Matlab: one beacon placed on one wall designated with coordinates of (0,0) and two beacons on the opposite wall with coordinates of (-243,-238) and (243,-238), approximately 16 feet apart. 100000 random coordinates were generated within the x range of [-243,243] and within the y range of [0,-238]. After using the generated coordinates to calculate the theoretical $r_i$ values, the equations mentioned were applied to these coordinates and the max error of the simulation was found as $~14.3cm$ which satisfies the constraint of localization within a precision of $15cm$

[The Matlab code used](https://github.com/Hawk652/Capstone-Guidance-Robot/blob/main/Software/Error_Calculations.m)

### Turtlebot:

#### LIDAR:
LIDAR sensors collect depth information about the environment using a laser. A laser is pulsed from the sensor and photons are reflected back to the sensor [8]. This allows the sensor to know the distance between itself and the surface from which the photons were reflected. The sensor spins and collects many points in order to gather depth information surrounding the sensor. The depth data gathered by the LIDAR sensor is sent to the Raspberry PI and then to the OpenCR 1.0 via a usb connection. The OpenCR 1.0 will then take the depth data and process it to send back to the Raspberry PI via a usb connection.

#### SLAM and ROS:
As the AuR moves, data points are collected by the LIDAR sensor and processed by a SLAM algorithm built into the ROS2, which is on board the TurtleBot3 [1]. The SLAM algorithm takes data points from the LIDAR and creates a model of the environment [8]. The SLAM algorithm uses incoming points to estimate the location of the TurtleBot3 by comparing the value of the points to their expected values and making corrections as needed. This process is described by the probability:

$P(x_k, m|z0_k, u0_k, x_0)$

Accuracy of SLAM is dependant on the quality of the LIDAR sensor but can have error as low as "5 cm given that LIDAR sensor depth accuracy already has 2-3 cm error" [9]. The type of SLAM algorithm used will also impact the accuracy of the model. This information means the constraints of being within 15 cm of the path and 1m of the destination, when used in conjunction with the UWB, can be fulfilled.

### Power:

The figure above shows the current draw for each component of the localization subsystem.

## BOM
| Item | Quantity | Price Per Item | Total Price | 
|-|-|-|-|
| OpenCR1.0 | 1 | $215.00 | Already Purchased | 
| Raspberry Pi3 B+ | 1 | $35.00 | Already Purchased |
| LDS-01 | 1 | $200.00 | Already Purchased |
| PLA Filament Roll | 1 | $24.99 | $24.99 |
| Buck Converter (2-pack) 12V to 5V Micro USB | 2 | $11.99 | $23.98 |
| Buck Converter (1-pack) 12V to 5V Micro USB | 1 | $7.99  | $7.99  |
| 9V Battery Connector (pack of 10) | 1 | $4.99  | $4.99  |
| ESP32UWB DW3000 | 5 | $43.80 | $219.00 |
| | | Total Subsystem Cost: | $280.95|
]
## References
[1] Y.  Name,  “ROBOTIS  e-Manual,”  ROBOTIS  e-Manual.  https://emanual.robotis.com/docs/en/platform/turtlebot3/slam/  (accessed  Nov. 09, 2022).  

[2] M. E. Rusli, M. Ali, N. Jamil, and M. M. Din, “An Improved Indoor  positioning Algorithm Based on RSSI-Trilateration Technique for Internet of Things (IOT),” 2016 International Conference on Computer and Communication Engineering (ICCCE), Jul. 2016, doi: 10.1109/iccce.2016.28.  

[3] M.  Simek,  “Two  Way  Ranging  (TWR),”  Sewio  RTLS.  https://www.sewio.net/uwb-technology/two-way-ranging/

[4]T. Polonelli, S. Schläpfer, and M. Magno, “Performance Comparison between Decawave DW1000 and DW3000 in low-power double side ranging applications,” IEEE Xplore, Aug. 01, 2022. https://ieeexplore.ieee.org/document/9881375 (accessed Nov. 28, 2022).

[5] Z. Li, X. Li, G. Mou, D. Jiang, X. Bao, and Y. Wang, “Design of  localization System Based on Ultra-Wideband and Long Range Wire-less,” 2019 IEEE 11th International Conference on Advanced Infocomm Technology (ICAIT), Oct. 2019, doi: 0.1109/icait.2019.8935892.

[6]DecaWave, “DW3000 Datasheet,” https://www.qorvo.com/. https://www.qorvo.com/products/d/da008142 (accessed Dec. 02, 2022).

[7]M. Farooq-I-Azam, Q. Ni, and M. Dong, “An Analytical Model of Trilateration Localization Error.” https://eprints.lancs.ac.uk/id/eprint/142930/1/PID1236902.pdf (accessed Dec. 09, 2022)..

[8] “What  is  LiDAR,  and  How  Does  it  Work?,”  J.D.  Power.  https://www.jdpower.com/cars/shopping-guides/what-is-LiDAR-and-how-does-it-work (accessed Nov. 09, 2022).  

[9] “The  definitive  guide  to  SLAM  &  mobile  mapping  technologies,” www.navvis.com.  https://www.navvis.com/technology/slam  (accessed Nov. 09, 2022).  

[10] Team  Ouster,  “Guide  to  evaluating  SLAM,”  ouster.com.  https://ouster.com/blog/guide-to-evaluating-slam/  (accessed  Nov.  9,  2022).

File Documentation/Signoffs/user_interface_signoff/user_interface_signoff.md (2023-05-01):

# User Interface Subsystem

## Functionality of the Subsystem
The user interface subsystem takes in voice input from the user and outputs audible feedback to the user. This subsystem will allow the user to input various commands to the AuR, such as "Go to room #" or "Stop". This subsystem will additionally notify the user when they have reached their destination or when an error has occurred. The user interface subsystem will be the primary means through which the user will interact with the AuR.

## Specifications and Constraints
| No. | Specifications and Constraints | Origin |
|-|-|-|
| 1 | Shall use voice assistant technology for user interface | Ethics |

## Buildable Schematic
schematic

The only hardware components of the user interface are the combination microphone and speaker. These will be connected via USB to the main control subsystem's Raspberry Pi. Both power and data with be transferred over this USB connection.

## Mounting
dimensions
mount

The microphone and speaker will be mounted to the AuR using a 3d-printed mount. The above images show the dimensions of the device and the model for the mount.

## Analysis

### Interface
The primary hardware component of the user interface subsystem will be a a conference microphone and speaker combination. This device will connect to the main control's raspberry pi, which will run Rhasspy, a voice assistant. Rhasspy was chosen because of its open source nature, configurability, and local processing capabilities [1]. We chose to use a voice assistant instead of another interface due to ease of user access. A touchscreen, the primary alternative to a voice assistant, would require the user to maneuver around a potentially moving robot in order to interface with it. This scenario would potentially be hazardous to a user, so the team has decided to implement a voice assistant instead.

### Power
The microphone and speaker are powered over a single usb type A connection. Unfortunately no documentation on the exact power specifications of the microphone and speaker were available, but the USB standard defines a voltage of 5 volts and a maximum current of 0.5 amps.

## BOM
| Item | Quantity | Price Per Item | Total Price |
|-|-|-|-|
| USB Speakerphone Microphone | 1 | $42.99 | $42.99 |
| | | Total Subsystem Cost: | $42.99 |

## References

[1] Rhasspy, “Rhasspy Documentation” Rhasspy Documentation. [Online]. Available: https://rhasspy.readthedocs.io/en/latest/. [Accessed: 01-Feb-2023].

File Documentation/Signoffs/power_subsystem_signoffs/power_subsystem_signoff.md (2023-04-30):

# Power Subsystem

## Function of the Subsystem
The function of the power subsystem is to recieve power from the docking station subsystem and distribute the power to the other subsytems. The power subsystem also has a battery monitoring system that will notify the main control subsystem when the battery charge fall below a certain threshold. 

## Specifications and Constraints

| No. | Specifications and Constraints | Origin | 
|-|-|-|
| 1 | Shall have plugless charging | Supervisor: Dr. Van Neste 
| 2 | Shall have a ripple voltage tolerance of 250 mVpp | Raspberry PI3
| 3 | Shall follow proper wire gauging standards | NEC 310.16(b)
| 4 | Shall not operate below 15-20% of the battery capacity | Ethics

## Buildable Schematic 


The system will recieve power from a pair of metal docking contacts. The battery distributes power to the rest of the system through a fuse box. The fuse box provides overcurrent protection to reduce the risk of electrical damage to the AuR's components. Buck converters are added to step down the voltage from 18V to 12V and reduces the ripple voltage cause by the motors. A manual switch is added between the fuse box and motors to reduce the safety risk of the AuR. The manual switch allows a user to immediately stop the AuR from moving and causing potential physical harm. The OpenCR1 provides 5 Volts to the RaspberryPI3, LIDAR, ESP32, and speakerphone using a built in voltage divider on the OpenCR1. The DDS Module is a componenet part of safety subsystem's design. The DDS Module will provide 5V to the ultrasonic sensors and near field sensors. For further information on the circuit for the sensors, refer to the safey subsystem. 
The voltage sensor will measure the voltage of the battery and send that measurement to the Raspberry PI3 located in the Main Control System

## Analysis
### Operating Current
Here are the operating currents for each of the devices on the AuR. 
| Device | <br>Max<br>Operating Current<br>(Amps) | Operating Voltage<br>(VDC) |
| --- | --- | --- |
| Ultrasonic Sensor 1 | 0.008 | 5 |
| Ultrasonic Sensor 2 | 0.008 | 5 |
| Ultrasonic Sensor 3 | 0.008 | 5 |
| Ultrasonic Sensor 4 | 0.008 | 5 |
| Near Field Sensor | 0.050 | 5 |
| RaspberryPI3 | 2.000 | 5 |
| LIDAR | 0.400 | 5 |
| ESP32 | 0.032 | 5 |
| Speakerphone | 1.500 | 5 |
| Voltage Sensor | 0.320 | 12 |
| Motors | 3.089 | 12 |
| OpenCR1 | 0.130 | 12 |

Using the equation below to transform current over converters and knowing that parallel currents sum up with each other, the total operating current can be calculated. 

$$\frac{I_p}{I_s} = \frac{N_s}{N_p}$$

$$I_s  = \text{secondary current (current on 5V)}$$

$$I_p = \text{primary current (current on 12V)}$$

$$N_s  = \text{secondary voltage (5V)}$$

$$N_p = \text{primary voltage (12V)}$$

$I_{s1} = 0.008 +0.008 +0.008 +0.008 +0.050 = 0.082 A$

$I_{p1} = I_{s1}(\frac{N_s}{N_p}) = 0.082(\frac{5}{12}) =  0.03412A$

$I_{s2} = 2.000 + 0.400+0.032+1.500 = 3.932  A$

$I_{p2} = I_{s2}(\frac{N_s}{N_p}) = 3.932(\frac{5}{12}) =  1.638A$

$I_M=\text{Motor Current} = 3.089A$

$I_{OCR}=\text{OpenCR1 Current} = 0.130A$

$I_{VS}=\text{Voltage Sensor Current} = 0.320A$

$\text{Total Max Operating Current} = I_M+I_{OCR}+I_{VS}+I_{p1}+I_{p2}$

$\text{Total Max Operating Current} = 3.089+0.130+0.320+0.03412+1.638$

$\text{Total Max Operating Current} = 5.212A$

Additionally, the converters are not perfectly efficient and has some loss. So, a 5% error is added to account for the converters' loss. 

$\text{Percent Error} = 0.05 * 5.212A = 0.261A$

After summing the current and performing the necessary calculations, the total operating current of the AuR is **5.212 ± 0.261A**. It is ideal for the AuR to be provided with about double the calculated operating to accomadate for future modifications and possible error. In conclusion, it is optimal for the battery to provide 10 Amps which is about double the calculated operating current.

### Ripple Voltage


The figure above shows the setup for simulating ripple voltage caused by the dc motor and how the designed filters reduce the noise caused by the motor. The goal of simulating the ripple voltage is to determine if the designed filters are able to keep the system within the constraint of having less than 250 mVpp for ripple voltage. The constraint is set at 250 mVpp due to the LIDAR and Raspberry PI3's max ripple tolerance of 5 ± 5\% V, which equates to 250 mVpp. So, the ripple voltage sent to components other than the dc motor must not exceed 250 mVpp to reduce risk of electrical damage. 

**Ripple Voltage Caused By Motor**


To create the motor, an inductor with series resistance is connected to a IGBT to represent motors turning on and off. A flyback diode is added to the motor's circuit to remove the sudden voltage spike caused when an inductor's current is cutoff. As seen from the graph, the simulated ripple voltage created by the motor is about 300 mVpp. This ripple voltage is higher than the constraint of 250 mVpp, which means that filters will be necessary.

**Voltage Output of 12V/5V Voltage Regulator**


The simulated ripple voltage outputted by the Voltage Regular is about 140 mVpp. Thus, the Voltage Regulator is able to keep the ripple voltage within the 250 mVpp constraint. So, no additional filters are necessary for the sensors.

**Voltage Output of OpenCR1 12V/5V Converter**


The simulated ripple voltage outputted by the OpenCR1 Converter is about 41 mVpp. Thus, the OpenCR1 Converter is able to keep the ripple voltage within the 250 mVpp constraint. So, no additional filters will need to be added at the OpenCR1's output. 

## BOM
| Item | Quantity | Price Per Item | Total Price |
| --- | --- | --- | --- |
| Battery INR-26650-5S2P | 1 | $135.00 | $135.00 |
| USB Cable | 2 | $6.00 | Already Purchased |
| Li-Po Battery Extension Cable | 1 | $9.00 | Already Purchased |
| Raspberry Pi 3 Power Cable | 1 | $8.00 | Already Purchased |
| Boat Rocker Switch | 1 | $6.00 | $5.99 |
| 6 Way Fuse Block | 1 | $12.00 | $12.00 |
| Metal Contacts | 1 | $16.95 | $16.95 |
| DIYmall Voltage Sensor | 1 | $5.59 | $5.59 |
| Buck Converters (2 pack) | 1 | $16.99 | $16.99 |
| | | Total Subsystem Cost: | $191.52 |

## References
“360 laser distance sensor LDS-01 (LIDAR),” _ROBOTIS_. [Online]. Available: https://www.robotis.us/360-laser-distance-sensor-lds-01-lidar/. [Accessed: 16-Feb-2023].

“Grove - ultrasonic distance sensor,” _Seeed Studio_, 29-Dec-2022. [Online]. Available: https://www.seeedstudio.com/Grove-Ultrasonic-Distance-Sensor.html. [Accessed: 16-Feb-2023].

“Raspberry pi 3 model B+.” [Online]. Available: https://static.raspberrypi.org/files/product-briefs/200206+Raspberry+Pi+3+Model+B+plus+Product+Brief+PRINT&DIGITAL.pdf. [Accessed: 16-Feb-2023].

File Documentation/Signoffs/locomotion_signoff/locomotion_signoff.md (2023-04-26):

# Locomotion Subsystem


## Function of the Subsystem
The locomotion subsystem is responsible for not only moving the AuR, but also maintaining the velocity set by the group in the constraints by using a closed loop system between the proposed motors, the encoders attached to those motors, and the controllers that will recieve feedback from the encoders. The feedback will go back to the Main Control subsystem to assist with the SLAM algorithm as well as re-adjust the duty cycle of the power signal being sent to the motors to maintain proper velocity.

## Constraints
| No. |Constraint  |  Origin  |
|-|-|-|
|1| Shall travel at a speed of 0.7 ± .1 m/s | Standard: ISO/TS 15066|

## Analysis
Based on the documentation provided by the Turtlebot3 manual, it is clear that the currently equipped motors do not provide the necessary torque to reach a velocity above .26 m/s. The replacement motors which we have been donated by the Mechanical Engineering Department should be more than powerful enough to reach and maintain the proposed velocity.

The starting point is to determine the amount of pushing force required to move the turtlebot using Newton's Second Law of Motion:

$f = m * a$

The mass of the unmodified turtlebot is 1.8kg. After removing the stock Dynamixel motors which weigh 40g a piece and replacing them with the Pittman GM9236S025, the mass comes out to be around 3.062kg. It would be safe to assume that the acceleration to the specified velocity will be close to instant for calculation's sake. $2.1434N = 3.062kg * 0.7\frac{m}{s^2}$

After calculating force, the following equation can be used to obtain the exact torque required by both motors combined using the force from the last equation along with the radius of the wheels of the AuR:

$T = (f * r_{wheel})$

$0.3537Nm = \frac{(2.1434N * .033m)}{2}$

The following equation will yield the current draw of the motors where $K_{T}$ is the torque constant of the motor found in the datasheet for the Pittman motor [1]:

$I = \frac{T}{K_{T}}$

$3.09A = \frac{0.03537Nm}{0.0229\frac{Nm}{A}}$

Last but not least, the power that the motors will be consuming running at their 12V operating point can be calculated using the following equation:

$P_{IN} = V * I$

$37.08W = 12V * 3.09A$

Based on the calculations above alongside the specifications provided to us via the datasheet of the motors, the group is certain that the motors that were provided will fit the needs of the AuR. They will not be operating out of spec and they also allow for overhead within the system for any future upgrades that would increase the mass of the AuR. The only downside to changing the stock motors is that now motor controllers are required to drive and regulate the speed of the motors. The Dynamixel motors that came stock on the turtlebot were an all in one closed loop system. Based on the calculations above, the Pololu Jrk G2 21v3 motor controller will be a perfect fit. Not only does it support a wide 4.5V-28V operating range, it can also deliver continuous current outputs of up to 2.6A. Each motor will be drawing ~1.545A. It also offers closed loop speed control to make use of the onboard motor encoders. Last but not least, the controllers are at a very solid price point for all that they offer at $59.50 per unit.[2]

## Pinout of the Motor Controller


This is the pin layout of the Jrk G2 21v3 motor controller.

## Buildable Schematic


This is how the locomotion subsystem will be powered and where the data that is retrieved is going. 

## BOM
| Item | Quantity | Price Per Item | Total Price | 
|-|-|-|-|
| Pittman GM9236S025 | 2 | $350.00 | Already Purchased |
| Pololu Jrk G2 21v3 | 2 |  $59.95 | $119.90 |
| Solder | 1 |  $10.00 |  $10.00 |
|Flux | 1 |  $10.00 |  $10.00 |
| | | Total Subsystem Cost: | $139.90|

## References
[1] GM9236S025, "GM9236S025.pdf" GM9236S025.pdf. [Online]. Available: http://www.gearseds.com/files/GM9236S025.pdf. [Accessed: 01-Feb-2023]
[2] Jrk G2 21v3 USB Motor Controller, "Jrk G2 21v3 USB Motor Controller with Feedback" Jrk G2 21v3 USB Motor Controller. [Online]. Available: https://www.pololu.com/product/3142 [Accessed: 01-Feb-2023]

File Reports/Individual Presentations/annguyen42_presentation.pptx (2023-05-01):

## Buck Converter


By Andre Nguyen

## What is a Buck Converter?

DC-to-DC converter that creates an output voltage lower than the input voltage.

## Not the Same

LM1117T-3.3/LD1117V33 Voltage Regulator LDO | Jameco

Voltage Regulator

Buck Converter

≠

Voltage ↓
Current ↓

Voltage ↓
Current ↑

## Not the Same

≠

Voltage Regulator

Voltage ↓
Current ↓

Buck Converter

Voltage ↓
Current ↑

## Not the Same

≠

Voltage Regulator

Linear

Buck Converter

Switching

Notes: Linear uses resistive load to step down voltage

Switcing stores energy and releases it periodically

## Main Components

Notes: Switch typically MOSFET or IGBT controlled by a PULSE WIDTH MODULE (PWM)

Inductor stores the current
Capacitor store the voltage

## How does the voltage decrease?

Voltage drop across the inductor
Closed Switch:
Input is the main source of power
Inductor charges
Opened Switch:
Inductor is the main source of power
Inductor discharges


## What is the Output Voltage?

Output Voltage Equation:
V_R = V_S ×D
V_S = Input Voltage
D = Duty Cycle

What is DUTY CYCLE in a linear actuator? | FIRGELLI

## What is the Output Voltage?

Output Voltage Example:
V_R = V_S ×D
V_S = 12 V
D = 0.50
V_R =12×0.50=6 V

## How does the current increase?

Closed Switch:
Current from voltage source
Opened Switch:
Current from the inductor
I_S < I_S + I_L
Over time, the average sum of the source and inductor current is greater than the source current alone

## How is the output energy steady?

Flywheel Circuit:
Allows the current to continuously flow even when the switch is open

## The Switch

Lower Frequency:
Efficiency ↑
Performance ↓
Higher Frequency:
Efficiency ↓
Performance ↑


## The Switch


Thermal at f_(SW) = 600 kHZ


Thermal at f_(SW) = 1000 kHZ

Thermal at f_(SW) = 600 kHZ

Thermal at f_(SW) = 1000 kHZ

## The Switch


Output Ripple Voltage at f_(SW) = 600 kHZ


Output Ripple Voltage at f_(SW) = 1000 kHZ

Thermal at f_(SW) = 600 kHZ

Thermal at f_(SW) = 1000 kHZ

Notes: Higher heat equal less efficient

## The Switch

Output Ripple Voltage at f_(SW) = 600 kHZ

Output Ripple Voltage at f_(SW) = 1000 kHZ

Thermal at f_(SW) = 600 kHZ

Thermal at f_(SW) = 1000 kHZ

## References

“Learnabout Electronics.” Buck Converters, https://learnabout-electronics.org/PSU/psu31.php.
The Organic Chemistry Teacher, director. Buck Converter. YouTube, YouTube, 20 June 2020, https://www.youtube.com/watch?v=rfChSvb8FX0. Accessed 5 Mar. 2023.
“Power Supply Technology - Buck DC/DC Converters.” Mouser Electronics, https://www.mouser.com/applications/power-supply-topology-buck/.
“Switching Regulator Fundamentals.” Texas Instruments, https://www.ti.com/lit/pdf/slvaed3.

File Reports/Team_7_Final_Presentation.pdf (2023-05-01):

Technology illustrations; by Storyset

# Autonomous Guidance Robot

Team 7: Andre Nguyen, Samuel Mandody, Jacob Wilkinson,

Gabriel Kim, Emma Brown

# Identify the Problem

The goal of the project is create an autonomous robot (AuR) that will guide people throughout the Ashraf Islam Engineering Building.


# Scope of the Project


Design the foundations of the AuR which includes the following:

- Localization
- Main Control
- User Interface
- Safety
- Locomotion
- Power

# Specifications and Constraints


- Detect the AuR’s position to a
precision of 15 cm
- Maintain a distance of 0.5 m from obstacles and people
- Guide users to within 1 m of their desired destination
- Use voice interface
- Travel at a speed of 0.7 土 0.1 m/s

# Full Block Diagram of the Entire System


# Turtlebot Waffle Pi

# User Interface


- The user interface must be easily accessible and must not require physical interaction with the AuR
- Voice control was the most efficient and effective option

# User Interface


- Consists of a microphone in addition to voice processing software running on a Raspberry Pi 3B+
- All processing is done locally on the Raspberry Pi

# User Interface


- Uses Rhasspy as an
intermediary layer
- Rhasspy allows easy
configuration and
consumption of voice
commands

# Localization Subsystem Design


- Collects depth data from the Lidar sensor
- Uses Lidar to form a map
- Can be given external reference coordinates
- Compares input data with a stored map to find its location


# Localization With UWB Beacons

- Measures distance using TDoA
- Calculate location using trilateration
- UWB beacon capabilities
- Official distance error of <10 cm
- Simulated beacon localization with matlab to ensure an error of <15 cm

# Substitute Beaconing System


- ESP32 Devkits
- BLE beacons
- RSSI Distancing

# Error Tests for BLE Beacons


- Max error of 1.2m
- High Variance
- NOT VIABLE


# Main Control Flow Chart

- Orange - Data
- Blue - States
- Green - Actions
- Yellow - Decisions

# Functions of the Main Control

- Used as a hub to tie all subsystems together


- Consists entirely of the Raspberry Pi
- Takes commands from the user interface

# Motor Schematic


# Why redesign an existing system?

- Constraints not met
- Existing components were very specific in compatibility
- System was not modular
- Difficult and expensive to service

# What are the most crucial features for our application?

Motor Controller (Jrk G2 21v3):


- Feedback loop input
- Compatibility with arduino interface
- Closed loop velocity control
- Overhead operating voltages and currents

Motor (Pittman GM9236S025):

- Rotary encoder output
- Power efficient
- Able to obtain and maintain velocity within reason

# Calculations for verification

- Newton’s second law
- Torque required per motor
- Current draw of the entire system
- Power draw of the entire system

# Power + Docking Station Subsystem


- Increase the power to meet
the specifications of added
components
- Provide electrical protection to the system
- Implement new charging
method

# Plugless Charging


- Increase autonomy
- Surface Mount Contacts
- Affordable
- Simple

# Safety Subsystem: Near Field Sensors


These sensors will be using a 360° obstacle avoidance technique which will determine the location of the obstacle.

As the sensors come into contact with an object, the voltage will decrease or increase depending on which coil is being triggered.

The coils that I used are in cross-sectional formation. This was to achieve detection at all corners of the robot.

# Near Field Sensor Schematic


# Circuit Schematic

Wheatstone bridges are used to measure very small changes in the environment
The op amp will amplify the resulting signal
The capacitors and the resistors will set the response time
The inductors are chokes and by implementing these are filtering out the high frequencies


# PCB Design


Image of the how the circuit was design and Implemented on a PCB breadboard

Simulated circuits before printing the PCB boards

# Cross Sectional Formation of Coils and Testing Process


Experimental Process
included two PCB boards

Two coils connect to each
circuit

Coils were within the
range of 3.35-3.45 of
Resonance frequency

Used variable resistors to balance the Wheatstone
Bridge circuit


### Videos of the Coils Functioning and Detecting

### Videos of the Coils Functioning and Detecting

### Video demonstrating the AuR’s navigation and user interface

# References

“Capacitive omnidirectional position sensor using a quarter wave resonator,” IEEE Xplore. [Online]. Available: https://ieeexplore.ieee.org/document/9827944

DecaWave, “DW3000 Datasheet,” https://www.qorvo.com/.https://www.qorvo.com/products/d/da008142

“GM9236S025.” [Online]. Available: http://www.gearseds.com/files/GM9236S025.pdf.

Rhasspy, “Rhasspy Documentation” Rhasspy Documentation. [Online]. Available: https://rhasspy.readthedocs.io/en/latest/

Y. Name, “ROBOTIS e-Manual,” ROBOTIS e-Manual. https://emanual.robotis.com/docs/en/platform/turtlebot3/slam/

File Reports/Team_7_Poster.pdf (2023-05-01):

Emma Brown, Gabriel Kim, Samuel Mandody, Andre Nguyen, Jacob Wilkinson

Abstract

The objective of this project is to design and develop a robot that can autonomously greet and guide people to their desired room within the new Ashraf Islam Engineering Building. The team’s objective is to establish the basic functions of the robot. The basic functions include safety, power, human interaction, and navigation.


Design

- User Interface - This is composed of a voice command system.
- Localization -The localization system was designed to provide the location of the robot within the building by utilizing the wireless beacons alongside a LIDAR.
- Main Control - The brains of the robot which is the Raspberry Pi.
- Locomotion - Consists of a motor control system.
- Safety - Composed of the near-field proximity sensors, which will detect objects that come into range of the robot and alert the system to stop.
- Power - Uses contact charging to recharge the robot and provide sufficient power to the robot’s systems

Experimentation & Results

We tested the robot's response to voice commands by providing spoken locations to the robot and observing that it moved to the desired locations. In order to test navigation and safety functionality, we placed obstacles and people in the environment surrounding the robot and confirmed the robot was able to avoid collision while navigating its environment.
To test location accuracy, we tested the accuracy of Bluetooth
beacon distancing instead of UWB and concluded that the error and variance of the measurements was too high to be a viable option for localization purposes.

Highlights


The motors ended up having the largest impact on the design. We lacked a mechanical background, so we did not have much knowledge on how to go about picking a motor. We figured out a roadmap for upgrading the motors with the help of Mr. Tristan Hill and learning a lot of new information regarding DC motors overall.


Specifications

- Navigate from one position to another position independently
- Locate itself with a positional error less than 15 cm
- Be controlled using voice commands
- Prevent collisions with people or obstacles as much as possible
- Recharge itself without the need of human interaction

Acknowledgements

The team would like to express thanks to Dr. Charles Van Neste for providing his guidance and knowledge through the course of the project. Additionally, thank you Dr. Andy Pardue for being the customer and providing the group another LIDAR sensor. Furthermore, special thanks to Tristan Hill and Dr. Stephan Canfield.

Future Work

Possible feature that can be included would be replacing the contact charging system with a wireless charging system. This would make it easier for the robot to charge itself without needing to be in an exact position and orientation. Another improvement would be the implementation of Ultrawideband beacons to increase the accuracy of the robot’s positional detection.

LIDAR Map of the First Floor of Prescott Hall

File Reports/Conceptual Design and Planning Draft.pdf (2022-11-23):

# Team 7: Conceptual Design and Planning

Andre Nguyen∗

, Emma Brown†

, Gabriel Kim‡

, Jacob Wilkinson§

, and Samuel Mandody¶

Department of Electrical and Computer Engineering, Tennessee Technological University Cookeville, TN
Email: ∗

annguyen42@tntech.edu, †

egbrown42@tntech.edu, ‡

gakim42@tntech.edu, §

jawilkinso43@tntech.edu, ¶sgmandody42@tntech.edu

I. INTRODUCTION
The goal of this project is to design an autonomous robot to greet and guide students and faculty members in the Ashraf Islam Engineering Building (AIEB). To achieve this goal, several systems will be utilized: main control, safety, localization, and power systems. The first is the autonomous aspect that the robot needs to have. This would include the robot knowing where it is and where it needs to go. The navigation and localization portion of the AuR will be using LIDAR for mapping, implementing a SLAM (simultaneous localization and mapping) algorithm, and using WIFI-beacons to track position. All these methods will ensure the robot’s awareness and the robot’s destination. The second challenge will be the power system. The power system will include a main battery using additional capacitors to reduce ripple voltage and overall noise. The battery will be charged using contact-based charging in order to ensure easy connection and disconnection from the power source. The last hurdle that will be encountered is the safety system. To ensure a safe environment for the robot and others that will be encountered by it, the safety system will use proximity sensors and speed detection. To solve the issues of these different systems, we have researched and determined the micro-controllers that we will be implementing.
A. Specs and Constraints
The specifications and constraints of this project ensure the safety of the robot and its surroundings. The robot should not cause any harm to anyone. There will be a safety system that will be implemented to ensure that precautions will be taken. Using preemptive collision sensors, there should be no running into walls, students, faculty, or objects. The team has also taken into consideration of how the robot will react to these potential collisions. The robot should stop until the sensors are no longer detecting the issue. The robot will also have wheels that are similar to a Roomba so that it can have a wide range of motion. The second constraint is the robot will guide the user to their destination. It will be using the SLAM algorithm to know how the hallways are laid out to know where it currently resides at and where it is going. There will be tracking methods that will be utilized to ensure that the robot reaches its final destination. The next specification the robot will have is it must easily leave and return to its home base without any assistance. To get this to work, the robot will have contact points that are powered by the home base. Contact based charging allows the robot to have a simple means of charging. The robot will have each major component be individually replaceable. This will help with future issues such as replacement parts and upgrades. These components will include the power systems, sensors, and the main control board. The constraints of the robot base will take up no more than 1.5 x 1.5 x 1.5 cubic meters of area. The reason behind this is the amount of space the robot will take up. The next constraint that the robot will have is to not deviate from the intended course by more than 15 centimeters in any direction. The battery life will last between 2-4 hours. This specific constraint was requested by our customer and the reasoning for this is because it needs to be active throughout the day. The final constraint that the robot will have is that the robot will move at an average walking speed. The average velocity of the AuR is about 0.7 ± 0.1 meters per second and the average walking speed is said to be equivalent to 0.82 meters per second [9]. This will ensure the safety of the robot and its surroundings. The team was given these constraints from 2 sources: the customer (Dr. Andy Pardue) and the team’s supervisor (Dr. Charles Van Neste). Here’s a breakdown of where specifically each specification/constraint originates from:
1) Dr. Andy Pardue
- The AuR shall guide the user to their destination.
- Battery life of 2-4 hours
- Speed of the AuR
- AuR charging station/Home base
- Modularity of the AuR
2) Charles Van Neste
- Collision detection
- Reaction time to collision
- SLAM algorithm
- Definite size
- Minimal error in movement and final destination. Further constraints are mentioned below.

II. BACKGROUND

A. Lidar

The LIDAR (light detection and ranging sensor) will gather various points of data from within the building by using a laser and sensor. In order for the LIDAR to determine how long it takes for the light from the laser to travel to a reflective surface and back to the sensor, these points will be fed into the SLAM algorithm to generate and save a map [2].

B. WI-FI and Bluetooth Triangulation

WiFi and Bluetooth triangulation make use of at least individual three access points to assess the location of a device [3]. Beacons are positioned in various locations with overlap, this is to ensure that no gaps are left. Based on the connected beacons, the location can be calculated by the device and strength of each receiving signal.

C. SLAM

SLAM is ”a method used for autonomous vehicles that lets you build a map and localize your vehicle in that map at the same time” [8]. SLAM works by taking information about the environment from visual sensors. Once this step is completed it will then processes the data. The purpose of this is to establish a consistent model of the environment. The position is also found in relation to that model. The input data is then compared to the existing model in order to reduce error.

D. Contact-Based Charging
A contact-based charging system consists of two metal tiles on the source and two metal tiles on the recipient. [1]. When the two receiving tiles make contact with the two source tiles, a circuit is formed and charging will begin. Contact charging is superior to plugin charging for autonomous purposes, since the system has a slower degradation rate. When the robot tries to make contact, there will be less of a chance for the system to become damaged.
While the AuR’s purpose is to benefit its’ users, the article ”Service Robots: A Systematic Literature Review” mentions potential mental health concerns as a result of emotional attachment to the AuR [4]. In order to address this concern, the speech of the AuR will be limited to non-colloquial phrasing such that the chances of emotional connection are reasonably diminished. The second response would be to communicate clearly with the user, that they have reached their destination. This would be indicating that the AuR is no longer paired with the user.

III. ETHICAL, PROFESSIONAL, AND STANDARDS CONSIDERATIONS
Profession ConsiderationsThe most prominent concern about the AuR is the impact that it will have on hallway congestion. In order to diminish this concern, the AuR will need to be in close proximity to the neighboring walls on the way to the destination. This is so that the robot will stay away from the central traffic in the hallway. To achieve this, the AuR will traverse the AIEB on the right side of the hallways.
Maintaining the AuR a is significant consideration that needs to be accounted for. This will affect TTU employees who will be working at AIEB due to increased maintenance. Maintenance of the AuR should be required as infrequently as possible to give employees more time for other tasks. Therefore, the AuR shall be modular so that general maintenance can be easily performed. Each individual major system shown in Fig. 1 will be as modular as possible.
A. Relevant Standards
There are many standards to be considered for this project. Some of the most prevalent ones include but are not limited to:
1) IEEE Standard 1873-2015: Room mapping uniformity
This standard aims to define common terms used to describe the areas where AuR is applicable (eg indoors, outdoors, the size of the space to be covered, etc.). This standard discusses the metrics used to describe the AuRs’ functionality as well. It also aims to classify the maps generated by AuR based on the data and the type of map used. The reason that we will be following this standard is because it will allow us to not only create a foundation for all automated robots that are developed for TTU in the future, but also it will help define the use case constraints of the AuR to high degrees of detail [5].
2) NEC Standard 310.16(b) Proper Wire Gauging
This standard was created to ensure that the proper wire gauge is used based on the temperature produced by the power flow. This standard becomes increasingly relevant to the project as the project approaches its final stage. During the initial stages, the team will be doing all algorithm-based testing using the prototype that was given to us by the customer. The prototype uses a low-power motor due to its small form factor relative to the intended final product. As power systems are implemented and low-power IoT devices are connected to relatively highpower DC motors, the team may encounter many fire-related safety issues if the standard is not strictly adhered to [7].
3) UL Standard 1642 Standard for Lithium Batteries
This standard covers the safety of lithium batteries (both rechargeable and non-rechargeable). It includes many rigorous stress tests that are performed on the battery/battery pack, this to ensure that it will not cause fires. If the team is going to be making our own battery pack, we will need to be following this standard closely for the testing of the pack; however, if we end up buying a battery pack, we will definitely need to ensure that the battery pack meets the standard [10].
4) ISO/TS Standard 15066 specifications of safety requirements for collaborative robot applications
This standard covers the safety aspects of the interaction of humans and robots. This is to ensure that any and all encounters are painless for humans. This is an important standard to keep at the forefront of our project throughout all of the stages. The AuR will be operating indoors and around people at all times. It is very important, that the robot will be unable to cause any bodily harm people that it interacts with[6].

IV. BLOCK DIAGRAM

A. Main Control

The main control system of the AuR will consist of the user input processing subsystem, the audio encoder, the notification system, the locomotion data encoder, and the navigation subsystem. These subsystems will be located on a Raspberry Pi model 3B. The input processing subsystem will receive location selection data from the user interface. This data will be sent to the navigation system which will then generate a route to the given destination. The audio encoder will process sound clips stored on the main control board to provide audible feedback to the user. The notification system will simply notify the staff of the AuR’s current position, received from the localization system, in the event the kill-switch is activated. The locomotion data encoder will convert route data received from the navigation subsystem into direct instructions usable by the locomotion system.
1) Navigation: The map data is obtained from the LIDAR component of the localization system and stored on the main control board. The pathfinding software will use the map data to create a path from the AuR’s initial position to the user’s desired position. This data will be sent to the localization control and the locomotion data encoder. If the AuR deviates from the initial route, the pathfinding software will receive new positional information from the route deviation detection module. With this new positional data, the pathfinding software will generate a new path to the user’s destination.
B. Localization System

The localization system consists of LIDAR, the localization control, and Bluetooth/WiFi beacons. The localization control subsystem will be driven by an ESP-S3 board. The localization control will receive positional data from the beacons and LIDAR system in addition to route data from the navigation system. Using this data, the localization control will compare the AuR’s current detected position with the expected position. If the detected position deviates from the expected position by more than 15 cm, then the localization control will send data regarding AuR’s current position to the navigation system, which will reroute the AuR from its current position. Furthermore, current position data will be continuously sent to the notification system of the main control board.


Fig. 1. Block Diagram

C. Safety System
The proximity detection system will be comprised of different sensors such as ultrasonic and infrared sensors. These proximity sensors will be continuously pulled for data that would indicate that an obstacle is obstructing the AuR. If the AuR detects an obstacle within 0.5 ± 0.1 m of itself, the safety system will notify the navigation subsystem that an obstacle is detected. In addition to the proximity sensors, a manual kill-switch will be included as part of the AuR’s safety system. This kill-switch will be a button or flip switch that will cut off power from the bus bar to the locomotion system if the user deems it necessary.
D. Power System
The charging system will use a contact-based charging method that will provide 1.5 ± 0.5 A at no more than 25 V. This is assumed for the charging system as the mechanical team has not provided further details regarding the load of the AuR’s motors. Further specifications of the battery will be determined later in the design process as more information is shared between the electrical and mechanical teams. The bus bar will be fed from the battery and will distribute power to the rest of the AuR’s systems. The bus bar will also have fuses to ensure that electrical damage from one system is isolated from the other systems.
E. User Interface
The user controls will consist of buttons that allow the user to input their desired location. This selected location data will be fed into the input processing portion of the main control. The sound output will be a speaker taking in data from the main control’s audio encoder. This data will be translated into sounds to provide audible feedback.
F. Locomotion
The electrical team will not be designing the locomotion system of the AuR. This responsibility has been given to the mechanical team.

Currently, little information has been received from the mechanical team regarding this system.

V. TIMELINE

The team used current deadlines that we were given in the Capstone class. As a team, we have added additional tasks and dates to ensure that everything will be completed in a timely manner. We have given ourselves an adequate amount of time between each to make sure that we have additional time in case something happens.
1) Design Phase 1: (9/27/2022-11/10/2022) : This phase consists of the Project Outline, TurtleBot Interfacing, Circuit Simulation, learning how to use and implement LIDAR, and Load Simulation the TurtleBot interfacing is going to be used to test our designs and theories to get a better idea of what we need to work on. The TurtleBot will be used for troubleshooting and testing. The circuit and load simulation will be the basics of how the hardware components will work and testing the process. LIDAR will be used in the mapping process and understanding how it works is important for the testing process that happens later. There will be a testing process this will consist of troubleshooting different algorithms with the TurtleBot and the LIDAR. Each of these sections will be distributed to different team members. The distribution can be seen in the accompanying Gantt chart.
2) Design Phase 2: (11/11/2022-11/21/2022) : This phase includes the design integration of the system and documentation. Design integration of a system will design the hardware components and how they interact with the software. There will be a testing process this will consist of troubleshooting the different components within the system. The documentation will be the paper of the design process written out into detail. These two categories are divided among the team members. The distribution can be seen in the accompanying Gantt chart.


Fig. 2. Gantt Chart of Project Timeline

3) Ordering Phase: (11/28/2022-1/25/2023) : This phase consists of the Wireless Charging Components, Sensors, Chips, Locality Components, and Miscellaneous necessities. This process will consist of finding, researching, and ordering the necessary components that will be needed for the robot. These categories are divided among team members. The distribution can be seen in the accompanying Gantt chart.
4) Development Phase: (1/26/2022-2/27/2023) : This phase consists of the Power System Integration, Safety System Integration, Location System Integration, and Final Assembly. The power system will contain the battery, wiring, and charging aspects that are needed for the robot. The power system should be able to keep the robot running for 3-4 hours. Safety system integration will include crash sensors and speed detection. This is to ensure the safety of the robot and the people it interacts with. Location system integration will include LIDAR, Wi-Fi beacons, Bluetooth beacons and other aspects of navigation. This will be the mapping and the brains behind the robot being able to have the awareness of where it is. The Final Assembly is piecing each of these components together. There will be a testing process will consist of troubleshooting the software components and the hardware components. As we test, the team plans to use different phases to accomplish goals that need to be met. These goals include testing in the Capstone Lab, testing in the hallway, and testing in the Laboratory Science Common Building. These categories are divided among team members. The distribution can be seen in the accompanying Gantt chart.
5) Revision Phase: (3/6/2023-4/3/2023) : This phase consists of the revision process of the entire project. As a team, we will make sure that all the documentation and the prototype is up to our standards for presenting.
6) Finalize Phase: (4/3/2023-4/22/2023) : This phase consists of the documentation and presentation processes. This will take the revisions we made and apply them. This final process is distributed amongst the team members. This item can be seen on the Gantt chart.

REFERENCES

[1] Automatic contact charging,” Skycharge.de. https://www.skycharge.de/technology. (accessed: Oct. 16, 2022).
[2] D. Bastos, P. P. Monteiro, A. S. R. Oliveira and M. V. Drummond, ”An Overview of LiDAR Requirements and Techniques for Autonomous Driving,” 2021 Telecoms Conference (ConfTELE), 2021, pp. 1-6, doi: 10.1109/ConfTELE50222.2021.9435580.
[3] F. A. Abed, Z. A. Hamza and M. F. Mosleh, ”Indoor Positioning System Based on Wi-Fi and Bluetooth Low Energy,” 2022 8th International Engineering Conference on Sustainable Technology and Development (IEC), 2022, pp. 136-141, doi: 10.1109/IEC54822.2022.9807489.
[4] I. Lee, “Service Robots: A Systematic Literature Review,” Electronics, vol. 10, no. 21, p. 2658, Oct. 2021, doi: 10.3390/electronics10212658.
[5] ”IEEE Standard for Robot Map Data Representation for Navigation,” in 1873-2015 IEEE Standard for Robot Map Data Representation for Navigation , vol., no., pp.1-54, 26 Oct. 2015, doi: 10.1109/IEEESTD.2015.7300355.
[6] “ISO/TS | 15066 | explained,” | Automate. | [Online]. | Available:
https://www.automate.org/tech-papers/iso-ts-15066-explained. [Accessed: 14-Oct-2022].
[7] M. W. Earley, J. S. Sargent, C. D. Coache, and R. J. Roux, National Electrical Code Handbook. Quincy, MA: National Fire Protection Association, 2014.
[8] Mathworks, “What Is SLAM (Simultaneous Localization and Mapping),” www.mathworks.com. https://www.mathworks.com/discovery/slam.html (accessed: Oct. 16, 2022).
[9] Murtagh EM, Mair JL, Aguiar E, Tudor-Locke C, Murphy MH. Outdoor Walking Speeds of Apparently Healthy Adults: A Systematic Review and Meta-analysis. Sports Med. 2021 Jan;51(1):125-
141. doi: 10.1007/s40279-020-01351-3. PMID: 33030707; PMCID: PMC7806575.
[10] R. Byczek and Name*, “Safety considerations for lithium and lithiumion batteries,” In Compliance Magazine, 12-Feb-2021. [Online]. Available: https://incompliancemag.com/article/safety-considerationsfor-lithium-and-lithium-ion-batteries/. [Accessed: 13-Oct-2022].

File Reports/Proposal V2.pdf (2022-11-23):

# Team 7: Autonomous Guidance Robot Proposal

Andre Nguyen∗

, Emma Brown†

, Gabriel Kim‡

, Jacob Wilkinson§

, and Samuel Mandody¶

Department of Electrical and Computer Engineering, Tennessee Technological University Cookeville, TN
Email: ∗

annguyen42@tntech.edu, †

egbrown42@tntech.edu, ‡

gakim42@tntech.edu, §

jawilkinso43@tntech.edu, ¶sgmandody42@tntech.edu

I. INTRODUCTION
The goal of this project is to create an efficient way for students and faculty members to be able to locate their classrooms within the Ashraf Islam Engineering Building (AIEB) by using safety, navigation, and power systems. Refer to Fig, 1 for an illustration of the project’s goal. Because the AIEB is currently under construction, this causes a couple of issues with the testing process that will be discussed within the proposal. The robot will solve the timeefficiency problem of people finding their destination. There are several goals and challenges that will be faced during the project, which include knowing where it is and where it needs to go, battery power runtime, and environmental safety system. The team has three electrical engineers and two computer engineers. The team has been divided into two different categories, one is the hardware team and the other is the software team. The hardware team will oversee the sensors, power system, and the safety system components. The software team will oversee the implementation of coding aspects of the project, such as mapping, security, and embedded systems integration. The project will be completed in the first week of April 2023. This will include the documentation, and the testing phases. The proposed budget is $1000, but this amount is subject to change due to implications or other necessities that are needed throughout the process. The team is eager to have a working prototype that can be modified for the next team to pick up where it left off.

II. FORMULATING THE PROBLEM
Due to the scope of the project, creating the autonomous robot (AuR) will require multiple specialized engineering teams.The chassis and locomotion of the AuR will be designed by a separate team of mechanical engineers working separately, with occasional communication, from this capstone project. The stakeholders for this project, as shown in Fig. 2, are Jesse Roberts, Dr. Van Neste, Dr. Pardue, the mechanical engineering team, and Tennessee Technological University. Jesse Roberts is the primary instructor for this capstone course. Dr. Charles Van Neste is the primary supervisor for this project. Tennessee Technological University, represented by Dr. Andy Pardue, is the customer for which the AuR is being designed.


Fig. 1. Vision of Project

A. Specifications and Constraints

Primarily, the AuR shall not cause harm to the user, bystanders, or any property during its standard operation procedures. The AuR shall ensure this specification is met using a multi-faceted safety system. This safety system shall include multiple redundant sensors, including positional and preemptive collision detectors, to ensure that there is no single point of failure. In the event that the AuR detects that it will collide with a person or object, the AuR will stop and will wait for that person/object to move. There will additionally be a manual shutdown switch that will cut power to the AuR and notify the staff of the AuR’s position.
Secondly, the AuR shall guide a user to the location the user selects then return to its home base. The AuR will only function on the first floor of the AIEB due to time constraints for this project. The AuR will primarily employ a custom simultaneous localization and map building (SLAM) algorithm in order to pathfind its way through the AIEB and bring the user to their destination. The AuR will have a positional error of no more than 1 meter from the location the user selects. In order to ensure that this positional constraint is met, the AuR will employ additional location tracking methods such as rangefinding from bluetooth beacons.
Additionally, the AuR shall be able to easily enter and leave its home base without a user’s assistance. In order to accommodate this, the AuR will be powered via contact points at its home base. Contactbased charging allows for easy connection and disconnection without concerns such as tangled wires.
In addition, the AuR’s major components shall all be independently replaceable. This independent replaceability means that if one major component is damaged or needs to be upgraded, that major component will be able to be replaced without needing to replace any other major components. These major components include the sensors, power systems, and main control board. This constraint is in place to ensure the AuR’s longevity through easy repairs and upgrades.


Fig. 2. Diagram of Stakeholders

The AuR’s home base shall not take up more than a 1.5 by 1.5 by 1.5 meter cubic area. This constraint is in place to ensure that the AuR has sufficient space to dock and charge while also ensuring that it does not take up the entire hallway.
The AuR shall not deviate from its intended course by more than 15 centimeters in either direction. This constraint will ensure that the AuR maintains a consistent and predictable path. The AuR will additionally be able to stay within a designated section of a hallway. The AuR’s battery shall last between two and four hours without charging. This constraint was requested by the customer in order to ensure that the AuR will be operational throughout the day.
The AuR shall move at a rate of 0.7 ± 0.1 meters per second. The slow walking speed for the average person is 0.82 meters per second, so a rate of 0.7 ± 0.1 meters per second ensures that the majority of users will be able to follow the AuR at a slow walking speed. [11]
B. Relevant Standards

There are many standards to be considered for this project. Some of the most prevalent ones include but are not limited to:
1) IEEE Standard 1873-2015: Room mapping uniformity
The standard aims to common terminology used to describe the areas in which an AuR is applicable (eg. indoor, outdoor, scale of space to be covered etc.) as well as the metrics used to describe the AuRs’ functionality. It also aims to categorize the maps genrated by the AuRs’ given the data above and the type of map used. The reason that we will be following this standard is because it will allow us to not only put together a foundation for all automated robots that are developed for TTU in the future, it will also help define the use case constraints of the AuR to high degrees of detail [5].
2) NEC Standard 310.16(b) Proper Wire Gauging
This standard is put in place to ensure that appropriate wire gauging is used based on the temperature being generated from power flow. This standard grows more pertinent to the project sooner it approaches the final stages. During the initial stages, we will be doing all algorithm-based testing using the prototype that was given to us by the ME team. The prototype is very low power and uses low power motors given its small form factor overall relative to the envisioned final product (refer to Fig. 1). As we implement the power system and connect the low power embedded system IoT devices to the much higher power DC motors, we could run into many fire related safety issues if this standard is not followed closely [9].
3) UL Standard 1642 Standard for Lithium Batteries
This standard covers the safety of lithium batteries (both rechargable and non-rechargeable). It includes many rigorous stress tests that are performed on the battery/battery pack to ensure that it will not cause fires. If we are going to be making our own battery pack, we will need to be following this standard closely for the testing of the pack; however if we end up buying a battery pack, we will definitely need to ensure that the battery pack meets the standard [13].
4) ISO/TS Standard 15066 specifications of safety requirements for collaborative robot applications
This standard covers the safety aspects of the interaction of humans and robots to ensure that any and all collaborations are painless for the humans. This is an important standard to keep at the forefront of our project throughout all stages. The AuR will be operating indoors around people at all times, so it’s important that the robot will be unable to cause any bodily harm to any individuals [6].
C. Challenges

The challenges the team may encounter fall into two categories: location-related challenges, supply-related challenges, time-related challenges, and customer-related challenges.
1) Location-Related Challenges: One challenge which may hinder testing is that the AIEB has not been fully built. If the construction of the AIEB is not completed by the testing phase, then the robot cannot be tested in its intended environment. This challenge can be mitigated by conducting the testing phase in the Lab Science Commons (LSC), which is the building most similar in structure to the AIEB.
2) Supply-Related Challenges: Another challenge which may hinder the building process is that essential components may not ship fast enough or in the worst-case may not be available. This challenge is mitigated by considering many different sources for the needed components as well as considering alternative components which are similar in function to the chosen ones.
3) Time-Related Challenges: Working with the mechanical engineering team may present the challenge of not having the chassis completed in time to build and test the AuR. This challenge can be mitigated by building an extremely basic chassis which can only support the essential functions and mobility needed to test the AuR and fulfil the Measures of Success.
4) Customer-Related Challenges: The customer has the option to request changes to the AuR specifications along the lifespan of the project. This may cause developmental issues due to specifications changing after they have been implemented. This challenge can be mitigated by giving the customer desired checkpoints, after which certain specifications cannot be changed.
D. The Measures of Success

The functionality of the AuR will be verified in a series of testing phases.
1) Phase 1: Phase 1 will focus on simulated data and non-physical tests and will be related to the battery, power systems, and circuitry of the AuR. Battery and power stability will be tested by conducting a noise simulation[7] on the circuitry in LT Spice. The test is successful if the input noise does not significantly affect the output noise. This shows that the noise from the power system should not significantly affect the components connected to the output of the power system. The power system circuitry will also be simulated with a range of loads to insure consistent power quality. The test is successful if the output voltage of the power system stays within a consistent range. This matters because the devices connected to the power source accept a limited range of voltages in order to operate consistently and accurately
The complete circuitry will be designed in KiCad and verified to ensure that there are no issues with the wiring and other related circuit construction. The test is successful if KiCad reports no errors when running a test on the circuit. This test will not flag any functional issues however, it will flag fatal circuitry issues.
2) Phase 2: Phase 2 will focus on testing individual systems and components.
The kill switch will be tested by connecting a power source in series with the switch, a resistor, and an ammeter. The switch will be toggled. The test is successful if toggling the switch to the open position produces a current reading of 0A ± 1µA. This ensures that the kill switch will shut everything down when toggled to the open position.

The lidar and SLAM algorithm will be tested by traversing the area of a room multiple times holding the lidar device. The data from each traversal will be compared to the data from the others and the real world information[16]. The test is successful if the test data is within an accuracy of ± 15cm and a precision of ± 5cm.
The power system will be tested by introducing a range of loads to the output of the power system and measuring the voltage across the load and current through the load. The test is successful if the voltage has low variance and the current stays within a safe range
3) Phase 3: The AuR will be set to traverse a simple room with stationary obstacles. The test is successful if the AuR correctly maps the room, avoids all obstacles, and can accurately know where it is within the room at any given moment.
The AuR will be set to travel in a straight line while obstacles move across the its path. The test is successful if the AuR reaches the end of its path while avoiding the obstacles.
4) Phase 4: In Phase 4 the AuR will be given a series of locations to navigate to within a hallway. The test is successful if the AuR accurately maps the hallway and successfully navigates, without collision, to every location.
5) Phase 5: In Phase 5 the AuR will be given a series of locations to navigate to the LSC. Obstacles will be placed around the floor and people will be walking around. The test is successful if the AuR accurately maps the floor and successfully navigates to every location. The AuR should also avoid all obstacles and people in the process.
E. Broader Implications, Ethics, and Responsibility as Engineers Although the AuR will provide great benefit to visitors of the AIEB, there are several resulting impacts that must be considered. Firstly, the AuR will increase congestion in the hallways while directing individuals due to its slow pace. The AuR will partially mitigate this increased congestion by returning to its home base between guiding visitors. The AuR can also mitigate this by setting its path along a wall out of the center of the walkway.
Secondly, maintenance of the AuR will potentially increase the workload for employees overseeing the AIEB. These maintenance issues will be partially alleviated by the planned modularity of the AuR. Employees will be able to easily swap out and upgrade malfunctioning and outdated components.
Aside from the direct impacts of the AuR, there are certain ethical considerations to take into account when developing a service robot. The McKinsey Global Institute estimates that ”half of today’s work activities could be automated by 2055”[10] and while this specific AuR concept is not directly displacing any current jobs, a development in this area of technology has the potential be applied to future AuR or service bots which do directly replace human labor. ”Service Robots: A Systematic Literature Review” notes the concern of human attachment to the robot[4]. While this AuR will is not designed with the intention of emotional influence there remains the possibility of emotional attachment and subsequent damage especially with ”vulnerable users such as the elderly with cognitive or physical disabilities”[4]. With this in mind guidelines for proper human-robot interaction must be established.

III. EXISTING SOLUTIONS
One solution is purchasing a commercial product that also achieves the specifications and constraints. For example, the artificial intelligence company Orion Star, offers several high quality AuRs that meet the expectations of the project. The expectations it meets includes having a default speed of 0.7 m/s and having a battery life of 12 hours, which exceeds our minimum requirements [3]. The disadvantage of using a commercial product is its high cost and reliance on third parties. Another existing solution to our objective is having dedicated personnel to perform greeting and guidance duties. Having personnel is a simple and effective way of meeting the project’s expectations. However, it is extremely cost-ineffective due to needing to provide hourly pay, benefits, and breaks. A third solution would be having several maps of the AIEB spread throughout the building. Maps would be a very cost-effective method of guiding people throughout the AIEB. Unfortunately, maps do not perform guidance duties and can be difficult for some people to utilize. Furthermore, maps do not meet several of the stakeholders’ specifications.
The AuR is broken down into three separate subsystems: navigation and location, safety, and power. The navigation and location system shall be responsible for traversing the robot through the AIEB while keeping track of its position. The safety system of the AuR is tasked with preventing any harm to any personnel and property. The power system provides a steady flow of power to the other systems at the rated voltage.
A. Navigation and Localization System
Unfortunately, the system is not able to utilize GPS signals due to it not being precise enough within an indoor environment. On the other hand, there are numerous methods that can be implemented in the design of the system. WiFi signal strength-based localization can be used to determine the position of the AuR within the AIEB. The AuR would run an algorithm that measures and records the strength of WiFi signals at various positions. By comparing previous measurements with current measurements of WiFi signal strength, the AuR is able to approximate its location. The downside of using WiFi signals to locate the AuR’s location is the inaccuracies due to objects and people creating interference with the WiFi signals [17]. An additional method that can be used for the localization and navigation system is applying a pathing algorithm that plans a route from the AuR’s current position to the objective location. The algorithm would create a path on a 2d map using multiple pathing templates. After creating the path, the AuR would follow a set of instructions created by the algorithm to reach the AuR’s final destination. As the AuR traverses the path, sensors would be used to track the AuR’s current location and compare the measured location with the predicted location of the AuR. If the algorithm detects that the AuR is not at the predicted location, the algorithm will use the real location to create a new path for the AuR. The pathing algorithm would be a simpler method of navigation compared to other existing methods. Additionally, implementing a pathing algorithm would be cost effective due to only needing a couple of cheap sensors to operate. However, using the pathing algorithm method for the system has some caveats. There could be times where the AuR could encounter a deadlock situation. The algorithm could also have trouble handling more complex layouts such as navigating different floor levels [14].
The LiDAR will provide the algorithm with scattered points which will be translated into vectors with accurate distance information to determine what obstructions surround the AuR /citething1. Using the map data in tandem withand extra information via external algorithms for the collision detecting and general pathing (ex. Matlab), the AuR will traverse the floor safely and effectively.
B. Safety System
Infrared sensors can be attached to the AuR to achieve collision avoidance. The sensors would obtain the orientation of the AuR and distance from objects in the environment. Then the data can be utilized to have the AuR stop before a collision occurs or go around encountered obstacles. The benefit of using infrared sensors is their low cost and simplicity of implementation. All though very effective, other methods of collision avoidance will be used to ensure reliability [8].
A hybrid method can also be used for the safety system design. The hybrid method utilizes both sensors and data from a map stored on an AuR. Sensors, such as ultrasonic sensors, would be used to detect new obstacles around the robot. The data from a map can be used to avoid known obstacles in an AuR’s path. Using map-based information for collision avoidance could reduce the need for expensive sensors to detect smaller obstacles in an environment. Having the AuR using the hybrid method for collision avoidance would be a very cost-effective way of adding redundancy to the safety system. The drawback of using the hybrid method is the need to have a highly accurate map stored on the AuR [2].
C. Power System
The power system can utilize wireless charging to supply power to the AuR. In a wireless power transfer systems, coils are used to transfer energy from one circuit to another without any form of contact. So, wireless charging would allow the AuR to recharge on its own, which means human intervention would not be necessary to charge the AuR. Wireless power systems would decrease the safety risks involved with power systems too. There would not be any exposed conductive material that can electrocute people. However, wireless charging is not the most efficient method of supplying power. The maximum efficiency of wireless charging is about 43%. If a wireless charging is implemented into the AuR, there would be concern about the misalignment between the coils used to transfer the power. This issue could be solved by using sensors and markers to keep the robot in alignment when charging. The major problem with using wireless charging is the cost of it. The cost of wireless systems would exceed the budget of the project by a large amount [12]. An alternative to wireless charging for the power system is contact charging. This method requires two pieces of conductive material to make contact with each other to transfer power from one circuit to another. It is a very simple method that can be used to supply power from a power source to the AuR. Contact charging is a more cost-effective option compared to wireless charging. The only concern with contact charging is safety. There would be an exposed piece of conductive material that can electrocute people. Some forms of safety measures would need to be implemented to prevent any harm [1].
A crucial concern with the power system design is the ripple voltage from the power supply. Ripple voltage can cause adverse effects on the AuR’s system. Some of the effects include interference and damage to the sensor systems. An acceptable tolerance for ripple voltage would be 100 mV peak to peak. To keep the ripple voltage within the tolerance, smoothing capacitors can be added. The values of the capacitors can be determined using equation 1 [15].

Vripple =

Iload
f × C

(1)

IV. THE RESOURCES

A. Personnel
The following list shows the team members’ skills that can be used for this project.


Fig. 3. Itemized Cost

1) Andre Nguyen
- Power System Analysis
- Soldering
- Leadership Skills
2) Emma Brown
- Knowledge of SMD/SMT Components
- Sensors
- Soldering
3) Gabriel Kim
- Arduino
- IoT Devices
- MQTT Protocol
4) Jacob Wilkinson
- Embedded Devices
- Soldering
- Software Development
5) Samuel Mandody
- Embedded Systems
- RTOS
- C Language
Additional skills that the team may need to successfully complete the project are KiCAD, 3D Printing, PCB Design, and machine learning.
B. Budget
The estimated material cost for this project is $810, as shown in Fig. 3. The costs are categorized by the subsystem they are a part of. The majority of these costs are from the power and navigation systems. Robust sensors and power supplies are needed in order to ensure the correct functioning of the AuR. These costs have been gathered by comparing prices from various manufacturers. The ”Unknowns” portion represents additional cost due to unforeseen complications such as shipping delays or extra components.


Fig. 4. Gantt Chart of Project Timeline

C. Timeline

The team used current deadlines that we were given in the Capstone class. As a team, we have added additional tasks and dates to ensure that everything will be completed in a timely manner. We have given ourselves an adequate amount of time between each to make sure that we have additional time in case something happens.

1) Design Phase 1: (9/27/2022-11/10/2022) : This phase consists of the Project Outline, TurtleBot Interfacing, Circuit Simulation, learning how to use and implement LIDAR, and Load Simulation the TurtleBot interfacing is going to be used to test our designs and theories to get a better idea of what we need to work on. The TurtleBot will be used for troubleshooting and testing. The circuit and load simulation will be the basics of how the hardware components will work and testing the process. LIDAR will be used in the mapping process and understanding how it works is important for the testing process that happens later. There will be a testing process this will consist of troubleshooting different algorithms with the TurtleBot and the LIDAR. Each of these sections will be distributed to different team members. The distribution can be seen in the accompanying Gantt chart.
2) Design Phase 2: (11/11/2022-11/21/2022) : This phase includes the design integration of the system and documentation. Design integration of a system will design the hardware components and how they interact with the software. There will be a testing process this will consist of troubleshooting the different components within the system. The documentation will be the paper of the design process written out into detail. These two categories are divided among the team members. The distribution can be seen in the accompanying Gantt chart.
3) Ordering Phase: (11/28/2022-1/25/2023) : This phase consists of the Wireless Charging Components, Sensors, Chips, Locality Components, and Miscellaneous necessities. This process will consist of finding, researching, and ordering the necessary components that will be needed for the robot. These categories are divided among team members. The distribution can be seen in the accompanying Gantt chart.
4) Development Phase: (1/26/2022-2/27/2023) : This phase consists of the Power System Integration, Safety System Integration,

Location System Integration, and Final Assembly. The power system will contain the battery, wiring, and charging aspects that are needed for the robot. The power system should be able to keep the robot running for 3-4 hours. Safety system integration will include crash sensors and speed detection. This is to ensure the safety of the robot and the people it interacts with. Location system integration will include lidar, Wi-Fi beacons, Bluetooth beacons and other aspects of navigation. This will be the mapping and the brains behind the robot being able to have the awareness of where it is. The Final Assembly is piecing each of these components together. There will be a testing process will consist of troubleshooting the software components and the hardware components. As we test, our team plans to use different phases to accomplish goals that need to be met. These goals include testing in the Capstone Lab, testing in the hallway, and testing in the Laboratory Science Common Building. These categories are divided among team members. The distribution can be seen in the accompanying Gantt chart.

5) Revision Phase: (3/6/2023-4/3/2023) : This phase consists of the revision process of the entire project. As a team, we will make sure that all the documentation and the prototype is up to our standards for presenting.
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

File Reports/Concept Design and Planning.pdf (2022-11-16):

# Team 7: Conceptual Design and Planning

Andre Nguyen∗

, Emma Brown†

, Gabriel Kim‡

, Jacob Wilkinson§

, and Samuel Mandody¶

Department of Electrical and Computer Engineering, Tennessee Technological University Cookeville, TN
Email: ∗

annguyen42@tntech.edu, †

egbrown42@tntech.edu, ‡

gakim42@tntech.edu, §

jawilkinso43@tntech.edu, ¶sgmandody42@tntech.edu

I. INTRODUCTION
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

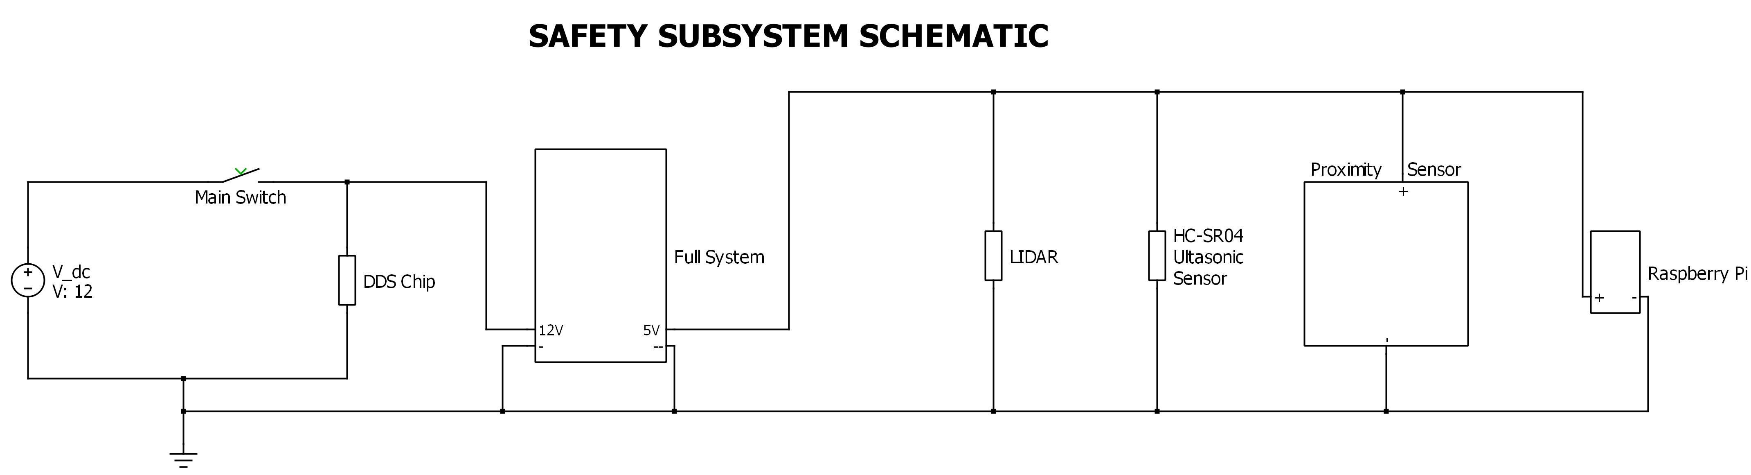
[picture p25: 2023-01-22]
Documentation/Images/safety/SafetySubsystemschematic.png

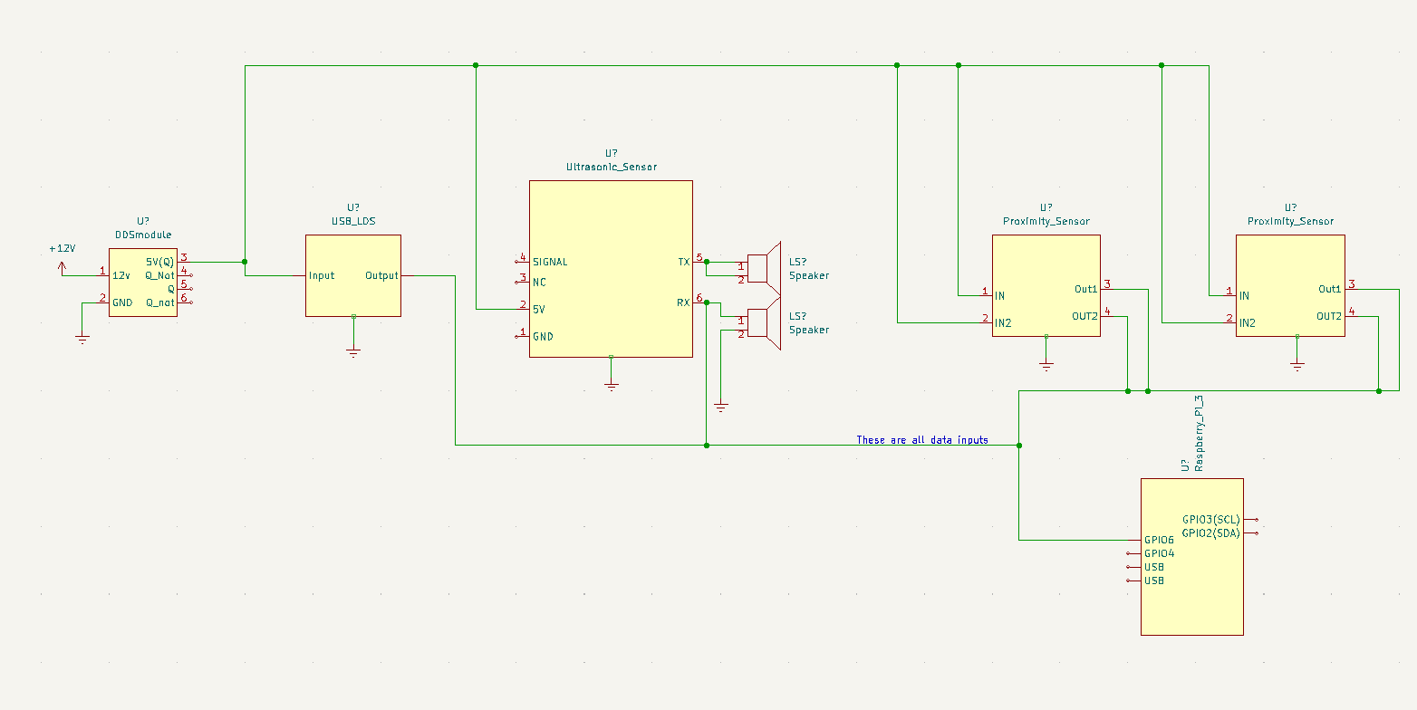
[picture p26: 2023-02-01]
Documentation/Images/safety/Pinout_diagram.png

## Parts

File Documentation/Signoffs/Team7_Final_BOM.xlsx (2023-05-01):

Name | Descripion | Subsystem | Part Number | Manufacturer | Quantity | Price | Total Price
Manual Switch | 5Pcs On/Off Boat Rocker Switch 5Pcs 2 Pin Position Snap 12V 110V 250V | Power Docking Station | B07Y1GDRQG | QTEATAK | 1 | $5.99 | $5.99
12V Power Supply AC Adapter | 12V 2A Power Supply AC Adapter, AC 100-240V to DC 12 Volt Transformers, 2.1mm X 5.5mm Wall Plug (12 Volt - 2amp - 2pack) | Docking Station | B077PW5JC3 | SmoTecQ | 1 | $17.99 | $17.99
Circuit Breaker | 30A-300A High-Current Circuit Breakers, Amp Breaker with Fuse Manual Reset Switch , 12-48V DC (30A) | Docking Station | B08GBYWFSC | allkpoper | 1 | $12.90 | $12.90
Dock Charging Contacts | Dock Charging Contacts Home Base for Roomba 500 600 700 800 560 595 650 770 780 | Power Docking Station | 8542024523 | caSino187 | 2 | $16.95 | $33.90
6 Way Fuse Block | 6 Way Fuse Block W/Negative Bus - ATC/ATO 6 Circuit Fuse Box with Ground, with Negative Bus & Protection Cover, Bolt Connect Terminals | Power | B08GJTS2Q2 | femedo | 1 | $11.99 | $11.99
Rechargeable Battery | 18V 10Ah (180Wh, 10A rate, 2x5S/S, INR-26650-5000) rechargeable battery | Power | INR-26650-5S2P | LiNiMnCo | 1 | $135.00 | $135.00
Voltage Sensor | Voltage Sensor Dc0-25v for Arduino | Power | B00NK4L97Q | DIYmall | 1 | $5.59 | $5.59
Speakerphone | USB Speakerphone Microphone, Conference Speaker Omnidirectional Computer Mic | User Interface | JV801 | JOUNIVO | 1 | $42.99 | $42.99
Motor Controller | Jrk G2 21v3 USB Motor Controller with Feedback | Locomotion | Jrk G2 21v3 | Pololu | 2 | $59.95 | $119.90
Solder | WYCTIN Diameter 0.6mm 100g 60/40 Active Solder Wire with Resin Core | Locomotion | BC-2045 | WYCTIN | 1 | $10.69 | $10.69
2 Jar Solder Flux | 2 Jar Solder Flux, Flux for Soldering, Rosin Soldering Flux Paste for Lead-Free Electronics Soldering and Soldering DIY | Locomotion | LF | Romeda | 1 | $7.98 | $7.98
DDS Module | DDS Module | Safety | 38504 | Dr. Van Neste Lab | 4 | $50.00 | $200.00
Grove | Grove-Ultrasonic Distance Sensor | Safety | SKU 101020010 | Seeed studio | 4 | $3.95 | $15.80
Motor Winding Wire | Motor Winding Wire 22Gauge,750 ft | Safety | 7588K79 | McMaster-Carr | 1 | $54.82 | $54.82
USB splitter | USB 3.0 Hub, VIENON 4-Port USB Hub USB Splitter USB Expander | Main Control | B09MLRPTT2 | vienon | 1 | $7.99 | $7.99
3D Printing Filament | 1.75mm Midnight Purple PETG 3D Printer Filament, 1 KG Spool, Dimensional Accuracy +/- 0.03 mm | Localization | 3D PETG-1KG1.75-MPUR | HATCHBOX | 1 | $24.99 | $24.99
9V Battery Connector | 9V Battery Connector,10 PCS T-Type 9 Volt Battery Buckle Connector Hard Buckle Plastic Shell | Localization | WCJ-9D-T-P15 | WEICHUANGJING | 1 | $4.99 | $4.99
Buck Converter | Direct Current Buck Converter Module 12V to 5V Micro USB Power Adapter (2pcs) | Localization | B08H89LTP5 | Weewooday | 1 | $11.99 | $11.99
Buck Converter | Direct Current Buck Converter Module 12V to 5V Micro USB Power Adapter (1pc) | Localization | B08Q34TYV5 | Weewooday | 1 | $7.99 | $7.99
Buck Converters (2 pack) | C-DC 5A Buck Converter 4-38V to 1.25-36V Step-Down Voltage Regulator High Power Module with LED Display | Power | B085T73CSD | Valefod | 1 | 16.99 | $16.99
Buck Boost Converter | DC DC Buck Boost Converter Variable Voltage Regulator CC CV 0.5-30V 4A 5V 6V 12V 24V Power Module Adjustable Voltage Regulated Laboratory Power Supply | Docking Station | B0978T3JKH | TKXEC | 1 | $20.88 | $20.88
ESP32UWB3000 | ESP32 UWB DW3000 Ultra Wideband Beacon | Localization | ESP32UWB3000 | Makerfabs | 5 | $43.80 | $219.00
 |  |  |  |  |  | Total Quantity: | 34
 |  |  |  |  |  | Total Price: | $990.36

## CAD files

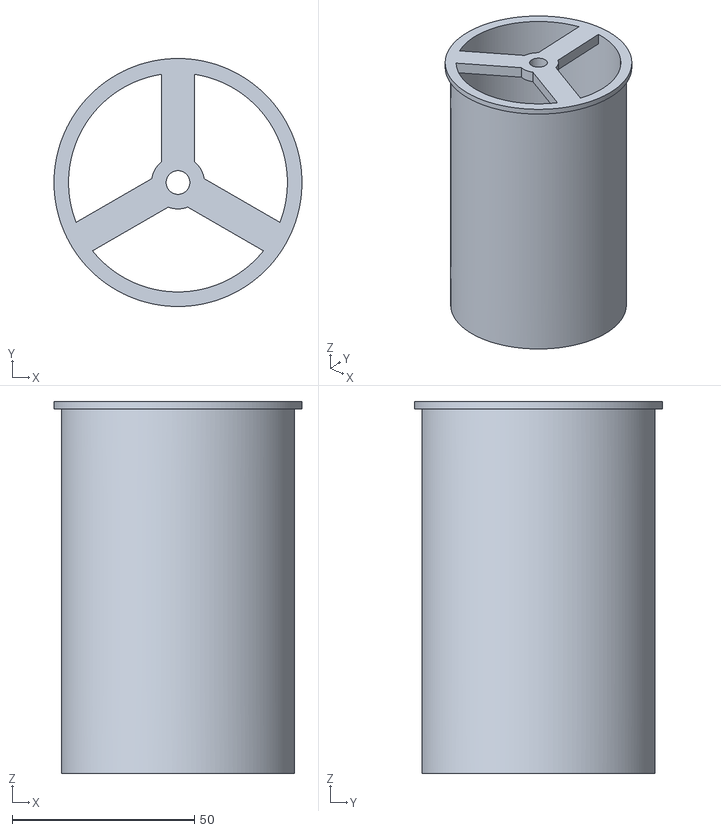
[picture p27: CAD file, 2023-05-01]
Documentation/3D Models/Bobbin-Emma.stl
68.0 x 68.0 x 102.0

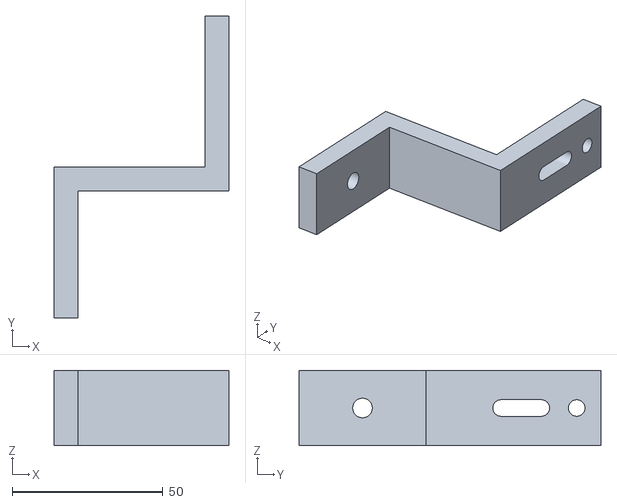
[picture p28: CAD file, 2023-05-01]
Documentation/3D Models/CoilBracketMount.stl
58.0 x 100.0 x 25.0

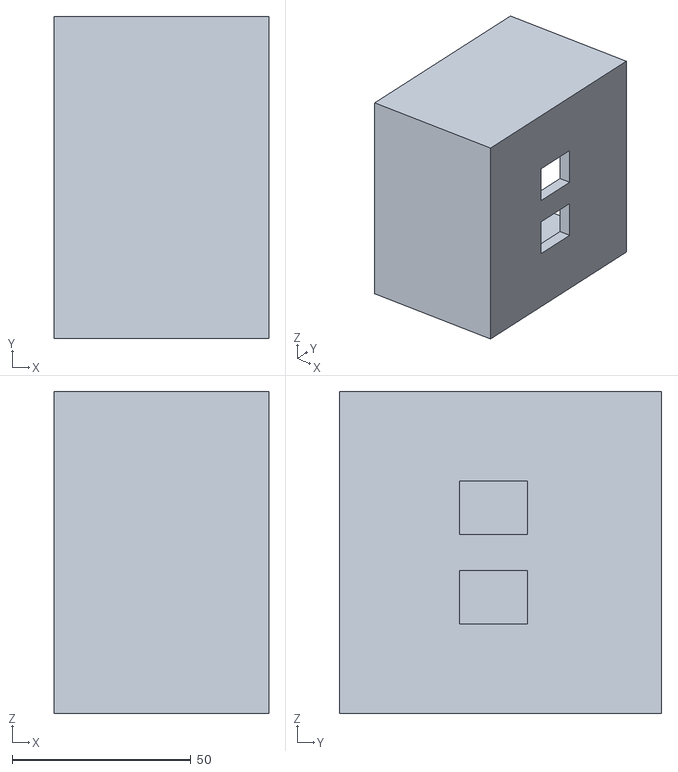
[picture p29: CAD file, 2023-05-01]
Documentation/3D Models/Docking_Station_Box.stl
60.0 x 90.0 x 90.0

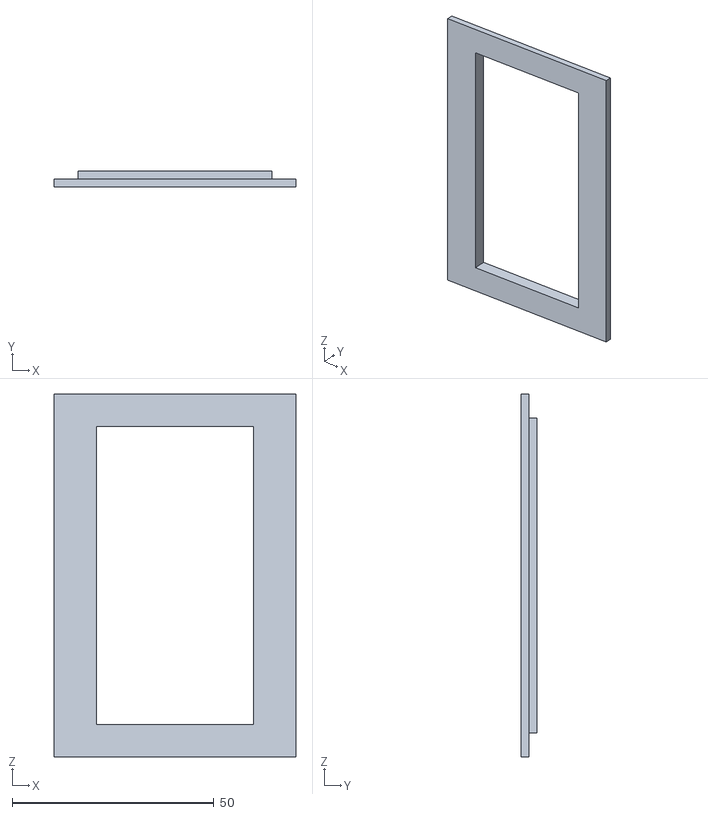
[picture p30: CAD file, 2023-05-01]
Documentation/3D Models/Docking_Station_Lid.stl
60.0 x 4.00 x 90.0

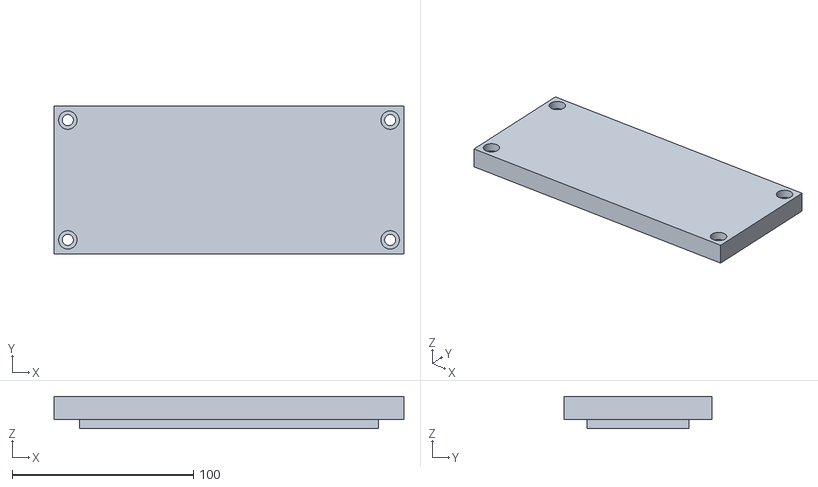
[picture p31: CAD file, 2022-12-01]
Documentation/3D Models/localization beacon box lid.stl
193.0 x 81.5 x 17.8

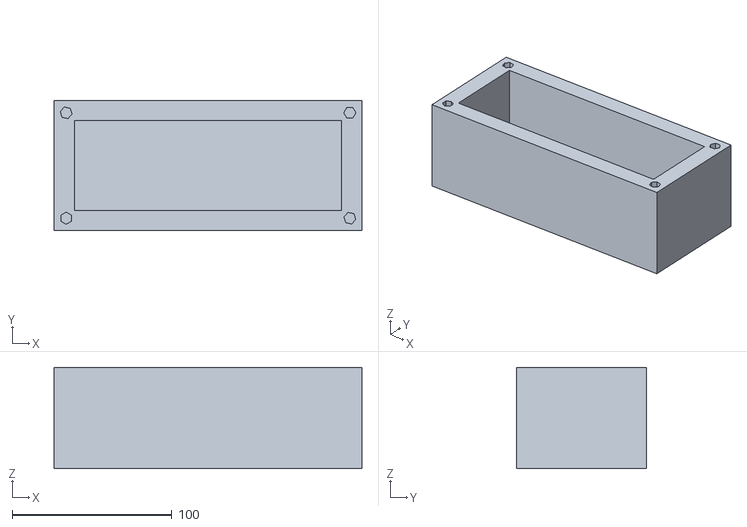
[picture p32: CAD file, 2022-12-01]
Documentation/3D Models/localization beacon box.stl
193.0 x 81.5 x 63.5

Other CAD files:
Documentation/3D Models/Bobbin-Emma.ipt
Documentation/3D Models/CoilBracketMount.ipt

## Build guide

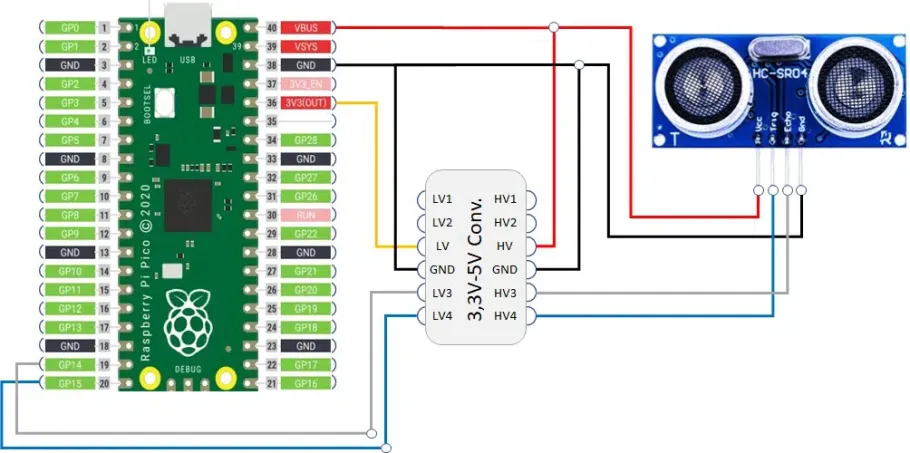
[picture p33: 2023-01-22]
Documentation/Images/safety/Raspberry-pi-pico-hc-sr04-wiring-diagram.webp

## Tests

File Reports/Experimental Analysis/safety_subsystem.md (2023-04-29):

# Analysis of the Safety Subsystem

## Safety Subsystem
The constraints below will not be achievable due to not having the designed battery and motors:
 - Shall have manual override (power will be cut from the motor)

 The constraint below will be tested because of the implementation of Lidar:
 - Shall maintain a distance of 0.5 m from obstacles and people
 
## LIDAR
### Testing Method
The test was performed by having the turtlebot navigate down the hallway of the first floor of Prescott Hall and having a person stand in the way of the turtlebot's path.

[Object/People Avoidance Experimentation](https://youtu.be/KBJQAzEwXu4)

### Result
The turtlebot was able to avoid collision with a person and wall. Unfortunately, the turtlebot did not meet the constraint of maintaining a distance of 0.5 m. For the turtlebot to maintain the distance of 0.5 m, additional sensors need to be added. 

Furthermore, 0.5 m is too large of a distance for the turtlebot to maintain. The turtlebot would not be able to navigate the hallways if there are obstacles in the way. The 0.5 m constaint should be adjusted since the hallways are too narrow and if there are multiple obstacles too.

## Proximity Sensor
- Was unable to test coils due to test due to delivery issues
- Printed out 3d models for bobbins for the coils
- If I were able to test this I would have tested the reasonance frequency and made sure that all of my turn were consistent. 

## Ultrasonic Sensor
- Was unable to test anything because these parts have not arrived 
- If I were to test this I would have tested the distance by placing an object in front of it, and seeing how long it would have taken for the information to be received. I would perform this task several times to ensure that the data was accurate.

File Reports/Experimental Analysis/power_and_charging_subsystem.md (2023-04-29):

# Analysis of the Power and Charging Subsystem

## Power Subsystem

The constraint below will not be tested due to not being able to implement the new motors for the project due to not having the motor controllers on hand:
 - Shall have a manual override switch
 
The constraints that will be tested are listed below:
 - Shall have a ripple voltage tolerance of 250 mVpp
 - Shall follow proper wire gauging standards

### Testing Method
To replicate the functionality of the battery connected to the power subsystem's circuit, a DC voltage supply is used to provide the power. The DC voltage supply is set to 18 V. Then the DC voltage supply is connected to the fuse box's positive and negative connections. A digital multimeter is used to measure the power output of the buck converters as the power supply sends power to the circuit. Additionally, a 1000 Ohm resistor is connected to the output of the buck converters so current can be measured. To measure the ripple voltage at the output, an oscilliscope was used to measure the output ripple voltage. 

[Ripple Votlage Experimentation Video](https://youtu.be/XyCeCxS2TAs)
 
### Results

The DC voltage and current at the output of the buck converters are listed below:
|  | Output Voltage (Volts) | Output Current (Amps)|
|--|--|--|
| Buck Converter 1 | 12.013 |0.12|
| Buck Converter 2 | 12.008 |0.11|

From measuring the output of both buck converters, the power subsystem will be able to provide the needed power for the additions that were planned for the robot initially. The measured ripple voltage is less than 250 mVpp. This was expected since the designed motors were not used. So, there is very minimal ripple voltage to begin with. The wires used for assembling the circuit were not overloaded.

The following constraints are related to the battery. However, since we did not recieve the desired battery, we will be testing the current LIPO battery on the turtlebot.
 - Shall have a battery life of 3-4 hours.
 - Shall not operate below 15-20% of the battery capacity. 

### Testing Method

To determine how long the battery will last, we ran the turtlebot and observed the capacity at different times. To determine if the turtlebot will operate below 15-20% battery capacity, we had the turtlebot move around until the motors stop moving due to low battery capacity. 

[Operation Below 15-20% Battery Life Experimentation Video](https://youtu.be/qoR8_F9Il6E)

The video explains the experimentation for ripple voltage. 

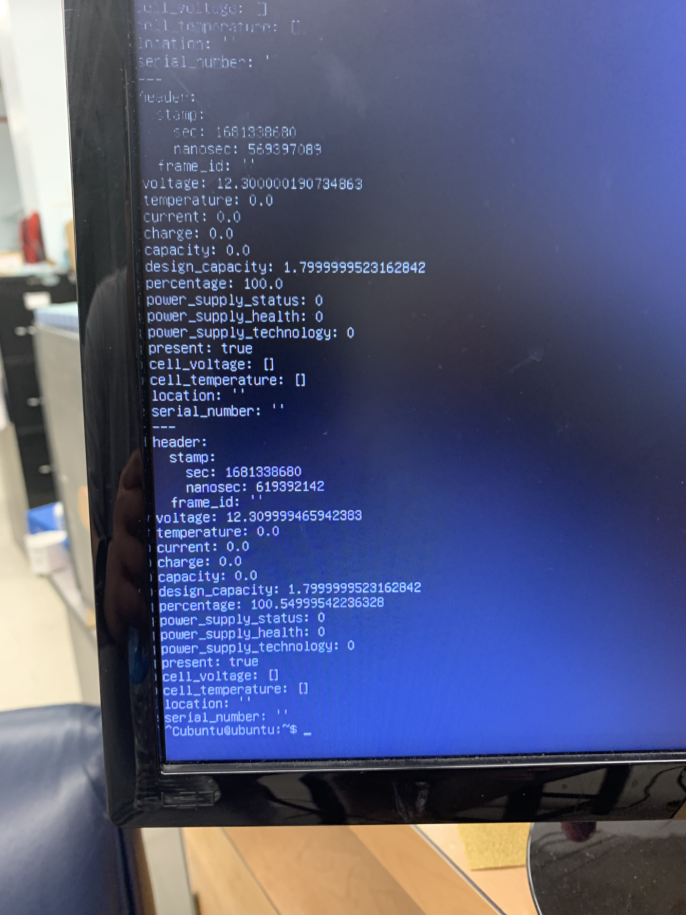
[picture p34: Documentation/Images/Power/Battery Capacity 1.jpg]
Battery Capacity at 100%


The figure above is taken at when the battery is 100%.

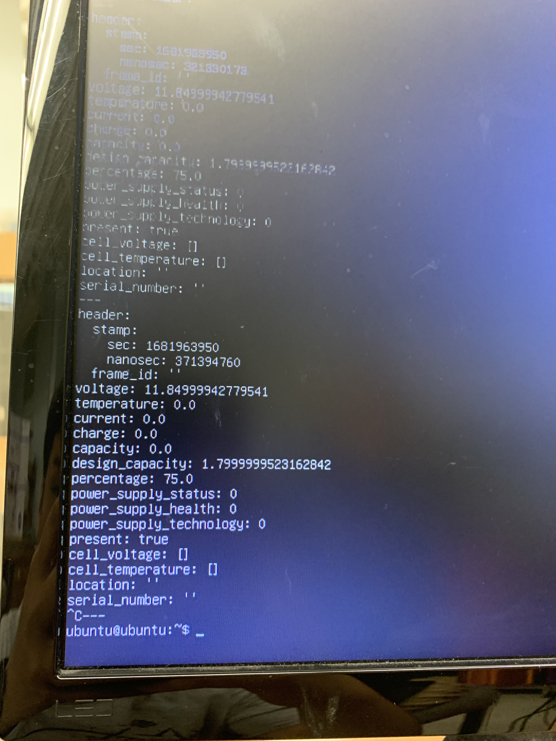
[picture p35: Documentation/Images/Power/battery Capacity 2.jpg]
Battery Capacity at 75%


The figure above is taken 30 minutes after the first figure. As you can see, the battery life is at 75%. 

### Results

The battery life of the LIPO battery while the turtlebot is functioning is around 2 hours. Additionally, if we added other componenets to the turtlebot, the battery life will be shorter. This means the constatint of 3-4 hours is not met. This is to be expected since the LIPO battery was not meant to be used in the final design. 

## Charging Subsystem

The constraints below will not be achievable due to not having the desired battery on hand and not being able to interface with the current LIPO battery:
 - Shall utilize plugless charging

The specifications and constraints that will be tested are listed below:
 - Shall follow proper wire gauging standards
 
### Testing Method

The charging system's circuit will be tested by connecting to a 120 VAC source such as a wall receptacle. Then a multimeter will then be connected to the metal charging contacts to ensure the correct DC voltage is provided. Additionally, the switch of the circuit will be toggled to ensure the circuit can be turned on and off by the user.

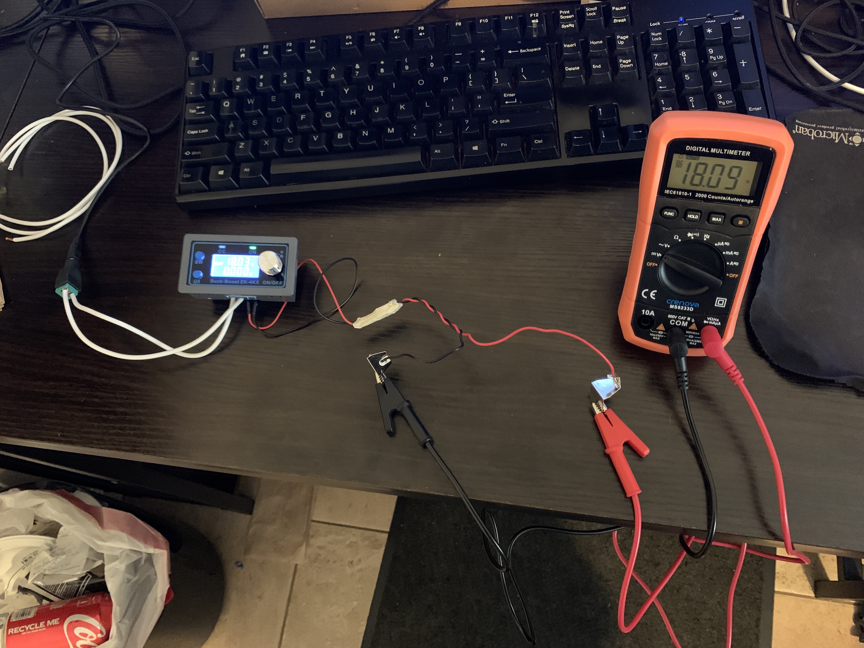
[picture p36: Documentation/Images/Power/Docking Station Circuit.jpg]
Docking Station Experimentation


The circuit is powered by a 120 VAC source. The circuit is supplying 18 VDC at the metal contacts. The switch on the Buck Booster can switch the output on or off.

### Results

After connecting the charging circuit to a wall receptacle, the multimeter read the following measurements at the metal charging contacts while connected to a 1000 Ohm resistor:
- Output Voltage: 18.1 VDC
- Output Current: 0.18 A

In conclusion, the charging subsystem's circuit functions correctly and can meet the required specifications. Furthermore, the output DC voltage can be adjusted due to the buck booster being adjustable. The switch to toggle the circuit on and off works properly too. The wires used for assembling the circuit were not overloaded.

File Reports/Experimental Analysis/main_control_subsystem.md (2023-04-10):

# Analysis of the Main Control Subsystem

## Main Control Subsystem
The constraint that will be tested is:
- Shall operate on one level

## Testing Method
In order to test proper operation, we first need to verify that the AuR can take data from the Lidar and use the data to form a map of a floor. The AuR must be able to navigate within the map without falling down or going up stairs. The testing location is floor 4 of Prescott hall.

## Results
We were able to map the fourth floor of Prescott Hall and have the robot move around to various points while avoiding the stairwell. This verifies that the constraint is met.

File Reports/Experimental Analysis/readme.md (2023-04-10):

# Experimental Analysis

The files in this folder are broken down by subsystem and provide insight as to why major components/design elements were selected. Alot of our design choices were based upon meeting specifications/constraints as well as keeping costs down overall wherever possible for the final product. The docmuentation for each subsystem not only explains what choices were made in the design phase, but also whether or not the implementation was successful or not and why or why not.

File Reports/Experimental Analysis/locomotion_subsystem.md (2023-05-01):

# Analysis of the Locomotion Subsystem

## Locomotion Subsystem
The constraints below will not be achievable due to not receiving motor controllers to drive the motors:
 - Shall travel at a speed of 0.7 m/s ± 0.1 m/s

### Experimental Methods
We ran an experiment of 5 trials to determine the top speed of the AuR. In these experiments, we marked a distance of 2 meters, accelerated the AuR to its top speed, then measured the time between crossing the two marked positions. This gave an overall average top speed of 0.23 m/s, which is within the expected range.

### Results

| Distance | Time |
|---|---|
| 2m | 8.52s|
| 2m | 8.75s|
| 2m | 8.68s|
| 2m | 8.56s|
| 2m | 8.53s|

Locomotion Experiment

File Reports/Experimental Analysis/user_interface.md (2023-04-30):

# Analysis of the User Interface Subsystem

## User Interface Subsystem
The constraints that will be tested are listed below:
 - Shall provide functional voice assistant interface 
 
### Testing Method
The user interface shall be tested by speaking commands and determining whether the AuR produces the appropriate response

### Results
After testing the "go to" command, the AuR correctly navigated to the given destination:
- Tested "go to room 119", AuR navigated to Prescott room 119
- Tested "go to elevator", AuR navigated to the elevator we set
- Tested "go to home", AuR navigated to the point we marked as its home

[Experimentation](https://youtu.be/yajVJaV24Pw)

In conclusion, the user interface subsystem functions correctly and is able to meet the required specifications.

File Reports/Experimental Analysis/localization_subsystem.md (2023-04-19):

# Analysis of the Localization System

## Localization Subsystem

The specification that will be tested is:

- Shall detect the AuR's position to a precision of 15cm  

### Testing Method

Since the originally decided UWB boards did not arrive in time, we decided to explore the possibility of bluetooth based positioning. We used two ESP32s for this test, one as a beacon and one as a reciever. Below is an account of the measurements and calculations used to test accuracy. We tested only distance error since positional error relies entirely on distancing error. 
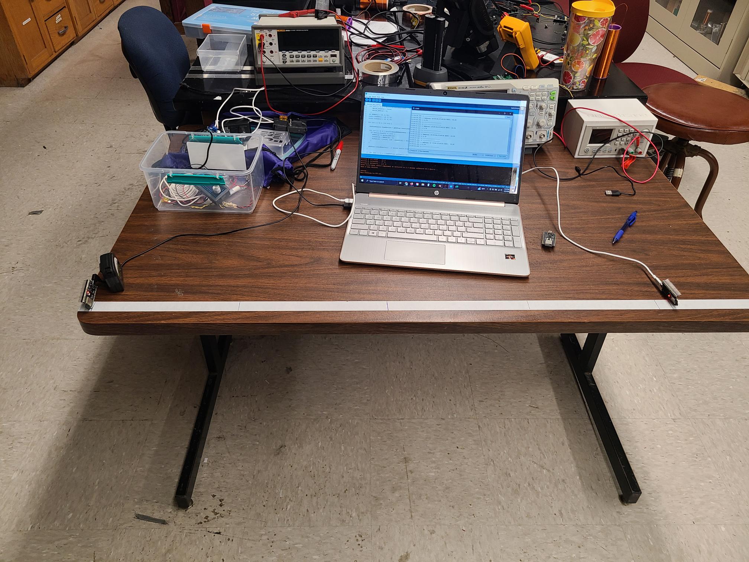
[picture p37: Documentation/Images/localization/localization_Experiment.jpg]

Figure 1: Experimental Setup
### Data

Each RSSI shown below is an average of 5 samples. Distance estimate is 

$$10^{\frac{Measured RSSI - InstantRSSI}{10N}}$$

[1] N is the natural constant which for which we use 4. The measured RSSI is the RSSI at 1 meter.

 #### RSSI at 1.00 meters
| RSSI: 1.00m |
| ---- |
| \-43 |
| \-42 |
| \-42 |
| \-43 |
| \-42 |
| \-42 |
| \-43 |
| \-43 |
| \-43 |  

Measured RSSI = -42.55555556

#### RSSI at 0.75 meters

| RSSI: 0.75m | estimate(m) |
| --- | --- |
| \-45 | 1.151094851 |
| \-47 | 1.291549665 |
| \-48 | 1.368078794 |
| \-48 | 1.368078794 |
| \-47 | 1.291549665 |
| \-48 | 1.368078794 |
| \-49 | 1.449142559 |
| \-49 | 1.449142559 |
| \-50 | 1.535009654 |
| Average: | 1.363525037 |
| Error: | 0.613525037 |  

#### RSSI at 0.5 meters

| RSSI: 0.5m | estimate(m) |
| --- | --- |
| \-41 | 0.914347141 |
| \-42 | 0.968525615 |
| \-41 | 0.914347141 |
| \-41 | 0.914347141 |
| \-41 | 0.914347141 |
| \-40 | 0.863199363 |
| \-41 | 0.914347141 |
| \-41 | 0.914347141 |
| \-41 | 0.914347141 |
| Average: | 0.914683885 |
| Error: | 0.414683885 |  

#### RSSI at 0.25 meters

| RSSI: 0.25m | estimate(m) |
| --- | --- |
| \-37 | 0.72629175 |
| \-37 | 0.72629175 |
| \-37 | 0.72629175 |
| \-38 | 0.769327242 |
| \-38 | 0.769327242 |
| \-37 | 0.72629175 |
| \-37 | 0.72629175 |
| \-38 | 0.769327242 |
| \-37 | 0.72629175 |
| Average: | 0.740636914 |
| Error: | 0.490636914 |

#### RSSI at 2 meters

| RSSI: 2m | estimate(m) |
| --- | --- |
| \-41 | 0.914347141 |
| \-39 | 0.814912747 |
| \-38 | 0.769327242 |
| \-38 | 0.769327242 |
| \-38 | 0.769327242 |
| \-38 | 0.769327242 |
| \-37 | 0.72629175 |
| \-37 | 0.72629175 |
| \-35 | 0.647308204 |
| Average: | 0.767384507 |
| Error: | 1.232615493 |

### Results

The errors presented are far too great to fit our constraint and are far too varied to correct. The positional error of trilateration is estimated to be greater than the distancing error. Our positional error constraint is under 15cm while our maximum error is above 1.2m. This is not a viable option.

## Sources

[1] R. Shah, “Convert RSSI Value of the BLE (Bluetooth Low Energy) Beacons to Meters,” BeingCoders, Jul. 26, 2021. https://medium.com/beingcoders/convert-rssi-value-of-the-ble-bluetooth-low-energy-beacons-to-meters-63259f307283

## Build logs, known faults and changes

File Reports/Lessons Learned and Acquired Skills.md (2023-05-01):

# Lessons Learned

## Gabriel Kim
### Reflections
Most of the designing and planning phase went well, but when it came to execution hardly anything went well. All of the problems were due to not getting the parts we needed to complete the project. In spite of all of this Dr. Van Neste was very helpful and understanding.
### Unanticipated Problems
The biggest unforeseen problem was not getting hardly any of the parts we needed to complete our project. I believe if we had gotten the needed supplies that we could have met most if not all of the specs and constraints.
### What I Would Redo
If I were to redo this project I would get the detail design phase done in the first semester so I could order the needed parts as soon as possible.
### Advice for Future Students
- Always have a backup plan
- Don't wait until last minute to do important things
- Understand that something will always go wrong
### Acquired Knowledge
- RSSI distancing is very inaccurate
- No amount of planning can make the impossible possible

## Samuel Mandody
•	The things that went well were the meetings and negotiations that we had with our stakeholders, advisor and customer. We always came prepared and had all our ideas lined up and thoroughly researched beforehand. Apart from that, honestly not too much. Due to the supply chain issue, we were not able to get our hands on any of the parts that we had ordered for our project.

•	Not having access to our parts made it difficult to figure out a direction since our entire project was dependent on having our parts. We tried seeing what we could substitute, but to no avail. There wasn’t much of anything we could do or show that the turtlebot wasn’t already capable of achieving.

•	If put in the same position of having to figure out what upgrades to implement or not, I would be sure to choose upgrades that are going to be more accessible parts wise at the tradeoff of writing more code or spending extra time optimizing the system overall.

•	Documenting everything is something that I have learned from this exercise overall. Had it not been for paper trails, we would not have been able to negotiate any. 

•	To any students reading this: Be sure that you make communication the most important facet of the project. Without it, you will not be able to get anything done in any reasonable amount of time. On top of not getting things done, you will end up with a lot of inner conflicts that sprout up due to the lack of communication. Keeping everyone in the loop at every step of the way is the key to success because if anything comes up at the last minute, everyone will be ready and able to contribute.

•	I learned how to use plecs for more detailed circuit simulation, how to use LaTeX for more professional looking documentation, and the fundamentals of DC motor physics.

## Emma Brown
The things that went well were that we always had our weekly meetings and discussed what was happening in our project with our stakeholders and supervisor. At the beginning, the group really struggled with communication and making each other know that everyone's opinions are important.

The biggest issue that we had was not recieving parts. Our project ended up not getting completed because of this hinderance.

If I were to do it all again, I think that I would double check to make sure that eveything had been ordered and if not what could I do to get that done. I wish that we had more time to figure out how to improve our designs. If we had a class before this to prepare us for capstone, I believe that would help the transition stage from being studnet to engineer.

Always have backup documentation, that way if anything were to happen you have evidence to prove what was said. Also, learn how to communicate with people, every person has a way they like to be communicated and just take that into consideration whether that be call, text, email and etc. In a professional setting, communication has been something that I have struggled with this semester and I think that I have improved significantly with this.

Future students, my advice would be start everything extremely early. During the semester, all of the other classes will become busy and you will feel as though you are drowning in work. If you go ahead and make a schedule for yourself, you will feel more at ease during capstone. Learn the importance of communicating with your team, the most important thing is to talk to your team. This is not an individual project, it is a group project. However, when you begin your subsystems that can be viewed as your contribution to the team.

I have learned how to design a circuit, design a PCB board and Surface Mount solder this semester. After completeing capstone, I feel very accomplished and proud of my contributions to the group. I have not only grown with my technical skills but also in my professional skills.

## Andre Nguyen

•    Reflect on the project, both technical and organizational. What went well? What didn’t go well?
  The team were able to complete tasks the sign offs within a reasonable time frame and collaborate well on tasks. What didn’t go well was some miscommunication between team members. Sometimes it was difficult to get in contact with team members at certain times. This made it difficult to complete some tasks.
  
•    What unanticipated problems occurred?
  Ordering was an issue I did not anticipate. The ordering issue made a major halt in the project’s progression during the second semester. I also did not anticipate how often team members would miss meetings due to different circumstances.
  
•    What would you do differently if you were to do it over again?
  I would have all sign offs complete before the second semester so parts would arrive in a timely manner. I would also change some of the constraints and collaborate more with a mechanical team so the scope of the project would be more reasonable. 
  
•    What “best practices” have you identified?
  One “best practice” was me creating a weekly agenda for the team. This sometimes kept the team updated on deadlines and assisted in team members coordinating with their tasks.  Another good practice was trying to keep consistency  between everyone’s work. 
  
•    What words of wisdom would you pass on to future students?
  It is important to keep up with the deadlines and attempt to not fall behind. Another advice is to always make an attempt even though it seems something will fail.
  
•    What new knowledge or skills did you acquire throughout capstone.
  I increased my knowledge of simulating different circuits. Additionally, I learned how to 3d model and print.
  
## Jacob Wilkinson

Reflect on the project, both technical and organizational. What went well? What didn’t go well?
From an organizational point of view, collaboration was good within the different sections of the team, however overall group-wide communication was lacking. We had a group leader who bridged the gaps between the different subgroups, but that resulted in most of the communication going through him. From a technical point of view, the design of the subsystems went well. However, most of the parts never arrived, so very few non-software subsystems were able to be implemented.

•    What unanticipated problems occurred?
The major unanticipated problem we experienced was our components not arriving. Outside of that, we had a couple issues with differing communication from our advisor and the course instructor regarding expectations for the project.

•    What would you do differently if you were to do it over again?
I would try to communicate more actively with my team. Most of the issues we encountered with the project were due to miscommunication between team members. I would also try to have more backup options available for when needed components don't arrive.

•    What “best practices” have you identified?
Weekly team meetings helped keep everyone on track, so they were a good practice to have. It's also good practice to document what you work on and let your other team members look over it.

•    What words of wisdom would you pass on to future students?
Communicate! Let your team members know what issues you're having and there will often be someone who can help! Also, for the sake of you and your team members' sanity, try to finish your part at least a couple days before the deadline instead of rushing to complete it at the last minute.

•    What new knowledge or skills did you acquire throughout capstone.
I worked mostly with the software of the AuR, so the main technical skills I learned were using and interfacing with ROS and the other software we used. From a soft skills standpoint, I learned better how to communicate and work with a team.

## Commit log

2022-11-21 Update Localization Subsystem.md
    updated the circuit schematic to properly represent the system
2022-11-21 Update Localization Subsystem.md
    updated the BOM to more accurately represent the subsystem's components
2022-11-21 Update Localization Subsystem.md
    added a figure of the current for the subsystem
2022-11-21 Update Localization Subsystem.md
    updated the BOM to better represent the components of the localization subsystem
2022-11-22 requesting signoff for power subsystem
    requesting signoff for power subsystem
2022-11-22 Update Main_Control.md
    Added current graph and redirected images to the correct directories
2022-11-28 Add files via upload
    Code flow diagram hosted image
2022-11-28 Update Localization Subsystem.md
    inserting code flowchart
2022-11-29 Changed lidar section and fixed reference order
2022-11-29 Update Localization Subsystem.md
    fixed the flowchart
2022-11-29 Update Localization Subsystem.md
    added schematic that shows the connections of the different components
2022-11-29 Update Localization Subsystem.md
    added the separate schematic of the wireless beacon
2022-11-29 Update Localization Subsystem.md
    added sentence to describe wireless beacon
2022-12-01 Update flowchart description
2022-12-01 Housing unit changes
    Added use case for the housing unit. Updated the bill of materials.
2022-12-01 Link + mark who's in charge of which subsystem
2022-12-03 LiDar is not a correct capitalization
2022-12-03 Add image of ESP32 UWB DW3000
2022-12-09 Added Main Control Flowchart
2022-12-09 Update Localization Subsystem.md
    updated the beacon schematic and provide a more detailed description
2022-12-09 Added Flowchart for Main Control
2023-01-25 Update Safety.md
    Added some more details on different sensors for my subsystem and added images
2023-01-29 Updated Main control schematic
    [Main_Control.kicad_sch]
2023-01-29 Updated Main Control Circuit Schematic
2023-01-29 Updated Power Calculations
2023-01-29 Updated Code Flowchart
2023-01-29 Added Updated Flowchart
2023-01-29 Added new flowchart
2023-01-29 Updated flowchart
2023-01-30 Update Safety.md
    added a different sensor that seems like it would work better with our system compared to the previous ultrasonic sensor
2023-01-31 Updated Analysis
    @DrVanNeste Please take a look and see if there are any ideas missing from the Analysis portion of my signoff barring the equations and schematics which will properly be added in once I have a body for a majority of the document.
2023-02-01 Updated BOM, OS, and Power sections
2023-02-02 updated power summary
2023-02-03 Update Safety.md
    added dds module and 3d schematic
2023-02-04 Update Power Subsystem.md
    added a new schematic of the power system's connections and included a description
2023-02-05 Update Docking Station Subsystem.md
    updated the BOM
2023-02-05 Update Power Subsystem.md
    updated BOM
2023-02-06 Update Power Subsystem.md
    updated the schematic and description
2023-02-06 Update Power Subsystem.md
    updated analysis portion
2023-02-07 Update Docking Station Subsystem.md
    updated the circuit schematic, descriptions, and BOM
2023-02-07 Update Docking Station Subsystem.md
    included model numbers and provided a description on how the devices will be mounted
2023-02-07 Update Docking Station Subsystem.md
    added further detail to mounting description
2023-02-08 Update Docking Station Subsystem.md
    updated the mounting description and graphics
2023-02-08 Update Power Subsystem.md
    updated schematic and BOM
2023-02-16 Update Power Subsystem
2023-02-16 Update Power Subsystem.md
    added the math equation showing how the max operating current of the system is calculated
2023-02-16 Update Power Subsystem.md
    made some gramatical changes
    added more to the ripple voltage analysis
    added some references
2023-02-17 Update Power Subsystem.md
    updated ripple voltage constraint
2023-02-17 Update Power Subsystem.md
    updated ripple analysis
2023-02-17 Update Power Subsystem.md
2023-02-17 Update Power Subsystem.md
    show the ripple voltage caused by the motor
2023-02-21 Update Power Subsystem.md
    updated the ripple voltage simulation and rewrote some of the descriptions
2023-02-21 Update Power Subsystem.md
    grammar
2023-03-09 Create Minimally Functioning Prototype.md
2023-04-13 Update Minimally Functioning Prototype.md
2023-05-01 Create power_subsystem_signoff
